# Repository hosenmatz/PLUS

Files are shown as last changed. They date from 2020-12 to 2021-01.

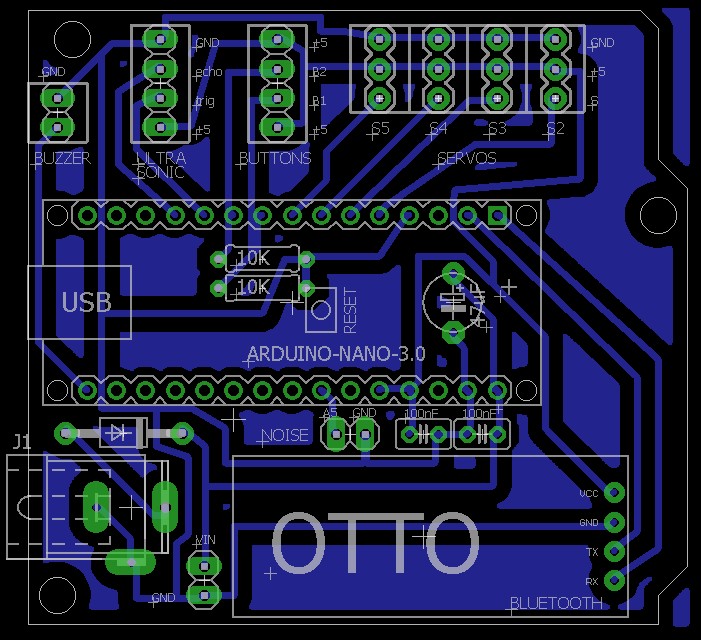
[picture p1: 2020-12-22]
PCB/PCB.jpg

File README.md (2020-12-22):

based on Arduino Nano clone from PRC

based on OTTO firmware v9

the PCB is a single sided PCB to be milled by a cnc with only THD-parts (CADSoft Eagle)

the serial connection is commented out because Bluetooth module is using the RX/TX Pins - means no controlling by wire

this way it is working with the OTTO DIY App now

<a title="bq, CC BY-SA 4.0 &lt;https://creativecommons.org/licenses/by-sa/4.0&gt;, via Wikimedia Commons" href="https://commons.wikimedia.org/wiki/File:Arduino-nano-pinout.png">Arduino-nano-pinout</a>

###

# Otto DIY+ (PLUS)

Special thanks to all these #Ottobuilder that made and are making this project evolve and accessible to everyoone in the world.

## License CC-BY-SA
<br /><span xmlns:dct="http://purl.org/dc/terms/" property="dct:title">Otto DIY</span> by <a xmlns:cc="http://creativecommons.org/ns#"  property="cc:attributionName"> [www.ottodiy.com](http://www.ottodiy.com) </a> is licensed under a <a rel="license" href="http://creativecommons.org/licenses/by-sa/4.0/">Creative Commons Attribution-ShareAlike 4.0 International License</a>.

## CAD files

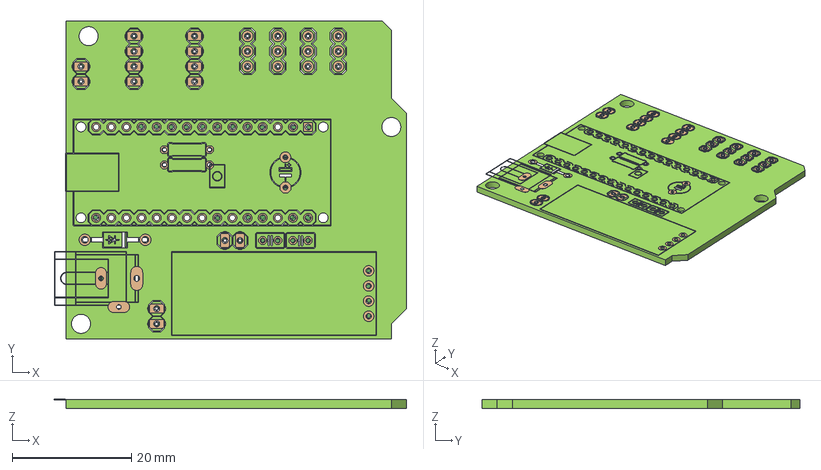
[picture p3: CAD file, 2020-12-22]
PCB/otto_single_sided.FCStd
59.1 x 53.3 x 1.57 mm
Board
Bottom_16
tPad_17
bPad_18
tPlace_21
tDocu_51

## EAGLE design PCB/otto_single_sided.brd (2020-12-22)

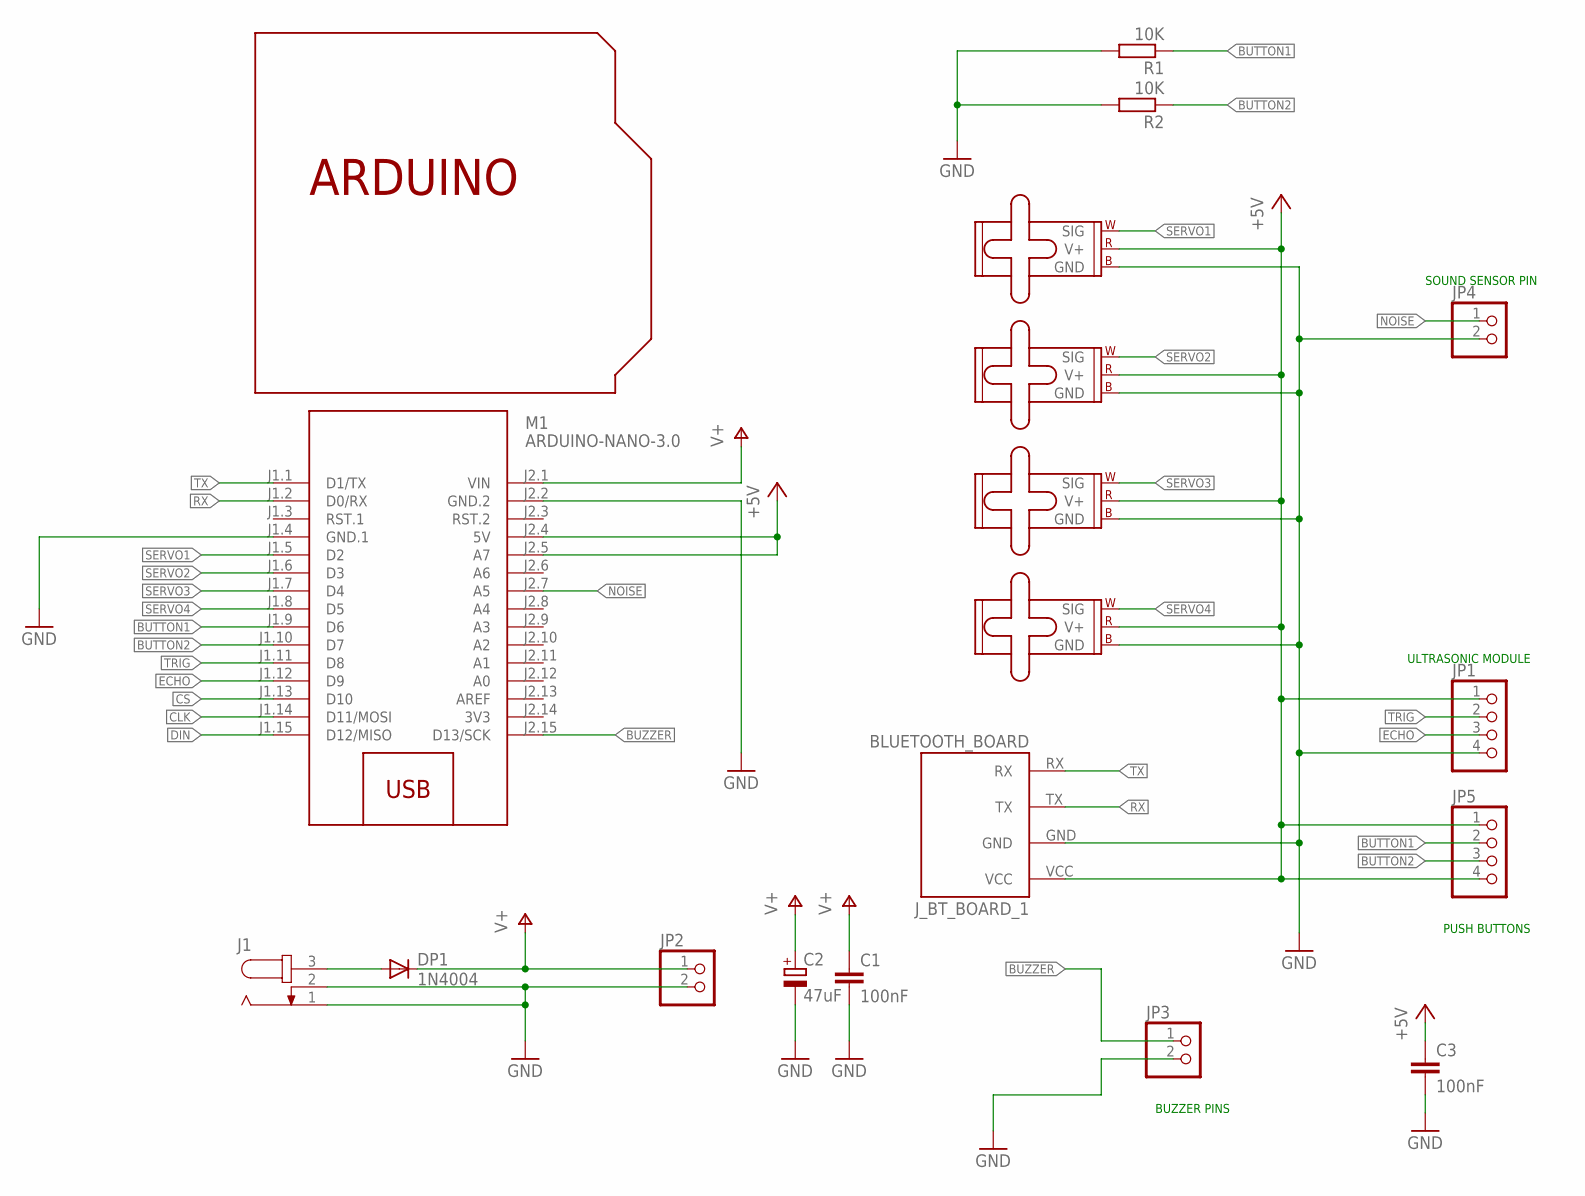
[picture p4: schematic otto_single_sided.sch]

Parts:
C1, C3: 100nF; C025-025X050
C2: 47uF; E5-5
DP1: 1N4004; DO41-10
J1: JACK-PLUG0; SPC4077
JP1, JP5: PINHD-1X4; 1X04
JP2, JP3, JP4: PINHD-1X2; 1X02
J_BT_BOARD_1: BLUETOOTH_BOARD; BT_BOARD_FOOTPRINT
M1: ARDUINO-NANO-3.0
M2, M3, M4, M5: SMALL_SERVO; 1X03
R1, R2: 10K; 0207/7
U$1: SHIELDSMALL; ARDUINOSHIELDSMALL

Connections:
3V3: M1.J2.14 (3V3)
+5V: C3.1, JP1.1, JP5.1, JP5.4, J_BT_BOARD_1.VCC, M1.J2.4 (5V), M1.J2.5 (A7), M2.2 (V+), M3.2 (V+), M4.2 (V+), M5.2 (V+)
BUTTON1: JP5.2, M1.J1.9 (D6), R1.1
BUTTON2: JP5.3, M1.J1.10 (D7), R2.1
BUZZER: JP3.1, M1.J2.15 (D13/SCK)
CLK: M1.J1.14 (D11/MOSI)
CS: M1.J1.13 (D10)
DIN: M1.J1.15 (D12/MISO)
ECHO: JP1.3, M1.J1.12 (D9)
GND: C1.2, C2.-, C3.2, J1.1, J1.2, JP1.4, JP2.2, JP3.2, JP4.2, J_BT_BOARD_1.GND, M1.J1.4 (GND.1), M1.J2.2 (GND.2), M2.3 (GND), M3.3 (GND), M4.3 (GND), M5.3 (GND), R1.2, R2.2
unnamed: DP1.A, J1.3
NOISE: JP4.1, M1.J2.7 (A5)
RX: J_BT_BOARD_1.TX, M1.J1.2 (D0/RX)
SERVO1: M1.J1.5 (D2), M2.1 (SIG)
SERVO2: M1.J1.6 (D3), M3.1 (SIG)
SERVO3: M1.J1.7 (D4), M4.1 (SIG)
SERVO4: M1.J1.8 (D5), M5.1 (SIG)
TRIG: JP1.2, M1.J1.11 (D8)
TX: J_BT_BOARD_1.RX, M1.J1.1 (D1/TX)
V+: C1.1, C2.+, DP1.C, JP2.1, M1.J2.1 (VIN)

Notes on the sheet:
ULTRASONIC MODULE
PUSH BUTTONS
SOUND SENSOR PIN
BUZZER PINS

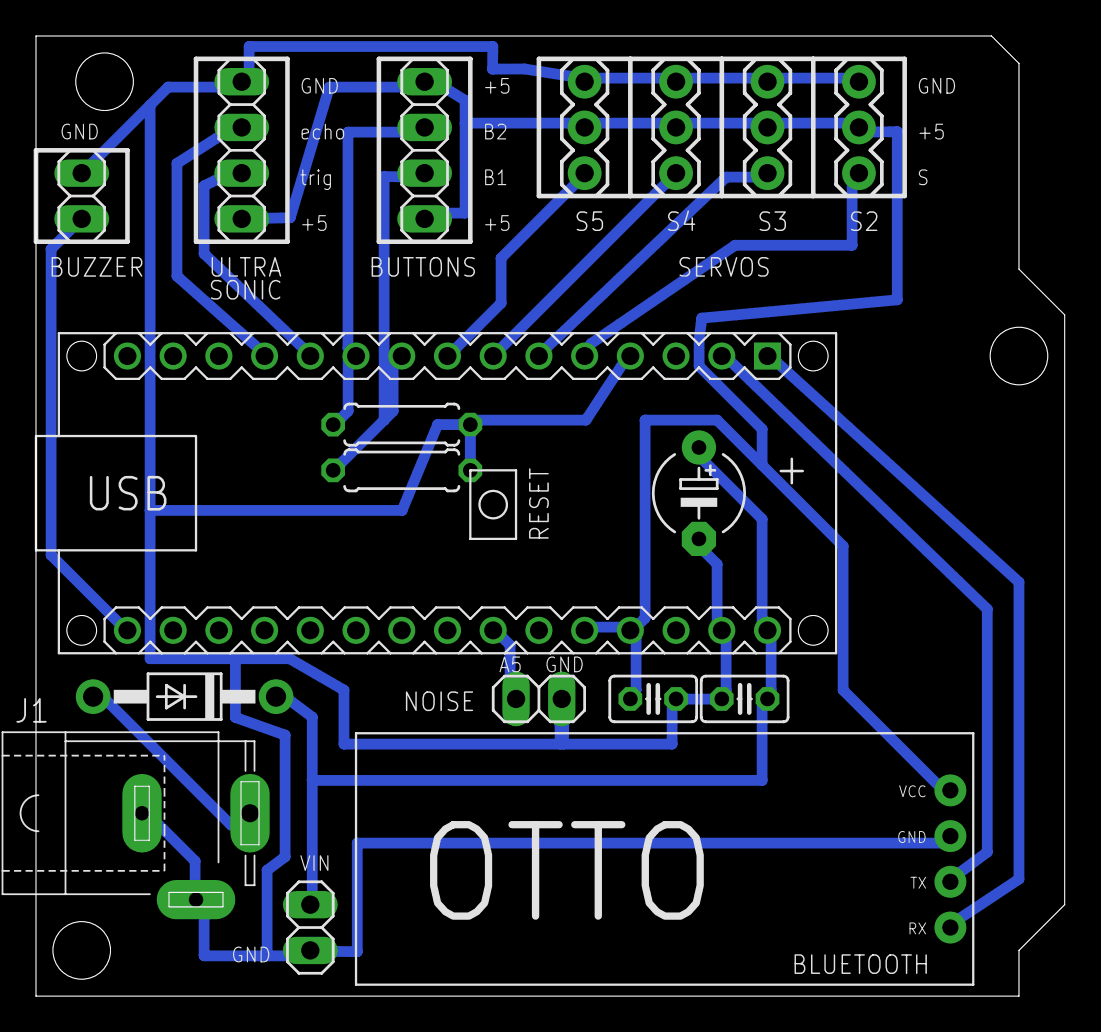
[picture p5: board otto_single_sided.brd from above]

Board: 2 copper layers, 57.2 x 53.3 mm, 19 parts (0 on the bottom side), 16 nets.

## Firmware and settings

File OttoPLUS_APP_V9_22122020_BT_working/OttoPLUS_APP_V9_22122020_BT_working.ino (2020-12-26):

//--------------------------------------------------------------------------------------------------------------------------------------------------------------------
//-- Otto DIY APP Firmware version 9 (V9) with standard baudrate of 9600 for Bluetooth modules.
//-- This code will have all modes and functions therefore memory is almost full but ignore the alert it works perfectly.
//-- Designed to work with the basic Otto or PLUS or Humanoid or other biped robots. some of these functions will need a good power source such as a LIPO battery.
//-- Otto DIY invests time and resources providing open source code and hardware,  please support by purchasing kits from (https://www.ottodiy.com)
//-----------------------------------------------------------------
//-- If you wish to use this software under Open Source Licensing, you must contribute all your source code to the community and all text above must be included in any redistribution
//-- in accordance with the GPL Version 2 when your application is distributed. See http://www.gnu.org/copyleft/gpl.html
//---------------------------------------------------------------------------------------------------------------------------------------------------------------------
// -- ADDED Progmem for MOUTHS and GESTURES: Paul Van De Veen October 2018
// -- ADDED PIN definitions for ease of use: Jason Snow November 2018
// -- ADDED Eye Matrix Progmem and control: Jason Snow November 2018
// -- REMOVED Eye Matrix Progmem and control: Jason Snow AUG 2019
// -- ADDED Battery meassurementin in mode 3 Jason Snow August 2019
// -- ADDED changed to original Software serial library Camilo Parra May 2020
// -- DELETED interrupts and modes to use BTserial Camilo Parra May 2020
//-------------------------------------------------------------------------
#include <EEPROM.h>
#include <SerialCommand.h>//-- Library to manage serial commands

//SoftwareSerial auskommentiert, da BT und Software die gleichen Ports teilen (RX/TX auf singlesided PCB auf dem Nano)
  //SoftwareSerial BTserial = SoftwareSerial(1,0); //  TX  RX of the Bluetooth - SoftwareSerial(rxPin, txPin, inverse_logic)
  //SerialCommand SCmd(BTserial);  //The SerialCommand object

SerialCommand SCmd;  //The SerialCommand object
#include <Otto9.h>
Otto9 Otto;  //This is Otto!
/*             -------- 
              |  O  O  |
              |--------|
  RIGHT LEG 3 |        | LEFT LEG 2
               -------- 
               ||     ||
RIGHT FOOT 5 |---     ---| LEFT FOOT 4    
*/ 
// SERVO PINs //////////////////////////////////////////////////////////////////////////////
#define PIN_YL 2 //servo[0]  left leg
#define PIN_YR 3 //servo[1]  right leg
#define PIN_RL 4 //servo[2]  left foot
#define PIN_RR 5 //servo[3]  right foot
// ULTRASONIC PINs /////////////////////////////////////////////////////////////////////////
#define PIN_Trigger  8  //TRIGGER pin (8)
#define PIN_Echo     9  //ECHO pin (9)
// BUZZER PIN //////////////////////////////////////////////////////////////////////////////
#define PIN_Buzzer  13 //BUZZER pin (13)
// SOUND SENSOR PIN //////////////////////////////////////////////////////////////////////////
#define PIN_NoiseSensor A6  //SOUND SENSOR   ANALOG pin (A6)
// LED MATRIX PINs //////////////////////////////////////////////////////////////////////////
#define DIN_PIN    A3   //DIN pin (A3)
#define CS_PIN     A2   //CS pin (A2)
#define CLK_PIN    A1   //CLK pin (A1)
#define LED_DIRECTION  1// LED MATRIX CONNECTOR position (orientation) 1 = top 2 = bottom 3 = left 4 = right  DEFAULT = 1
// BATTERY SENSE PIN //////////////////////////////////////////////////////////////////////////
boolean BATTcheck = false;    // SET TO FALSE IF NOT USING THIS OPTION
#define PIN_Battery   A7  //3v7 BATTERY MONITOR   ANALOG pin (A7)
// TOUCH SENSOR or PUSH BUTTON /////////////////////////////////////////////////////////////////
#define PIN_Button   A0 // TOUCH SENSOR Pin (A0) PULL DOWN RESISTOR MAYBE REQUIRED to stop false interrupts (interrupt PIN)
// SERVO ASSEMBLY PIN   /////////////////////////////////////////////////////////////////////
// to help assemble Otto's feet and legs - wire link between pin 10 and GND
#define PIN_ASSEMBLY    10   //ASSEMBLY pin (10) LOW = assembly    HIGH  = normal operation
///////////////////////////////////////////////////////////////////
//-- Global Variables -------------------------------------------//
///////////////////////////////////////////////////////////////////

const char programID[] = "OttoPLUS_V9"; //Each program will have a ID
const char name_fac = '$'; //Factory name
const char name_fir = '#'; //First name
//-- Movement parameters
int T = 1000;            //Initial duration of movement
int moveId = 0;          //Number of movement
int moveSize = 15;       //Asociated with the height of some movements
volatile bool buttonPushed=false;  //Variable to remember when a button has been pushed
unsigned long previousMillis = 0;
int randomDance = 0;
int randomSteps = 0;
bool obstacleDetected = false;
double batteryCHECK = 0;
unsigned long int matrix;
unsigned long timerMillis = 0;
///////////////////////////////////////////////////////////////////
//-- Setup ------------------------------------------------------//
///////////////////////////////////////////////////////////////////
void setup() {
  //Serial communication initialization
  Serial.begin(9600);
  //SoftwareSerial auskommentiert, da BT und Software die gleichen Ports teilen (RX/TX auf singlesided PCB auf dem Nano)
  //BTserial.begin(9600);

  Serial.println("AT+DISC");
  
  Otto.init(PIN_YL, PIN_YR, PIN_RL, PIN_RR, true, PIN_NoiseSensor, PIN_Buzzer, PIN_Trigger, PIN_Echo); //Set the servo pins and ultrasonic pins
  Otto.initMATRIX( DIN_PIN, CS_PIN, CLK_PIN, LED_DIRECTION);   // set up Matrix display pins = DIN pin,CS pin, CLK pin, MATRIX orientation 
  Otto.matrixIntensity(1);// set up Matrix display intensity
  Otto.initBatLevel(PIN_Battery);// set up Battery percent read pin - MUST BE AN ANALOG PIN
  randomSeed(analogRead(PIN_NoiseSensor));   //Set a random seed
  pinMode(PIN_ASSEMBLY,INPUT_PULLUP); // - Easy assembly pin - LOW is assembly Mode
  pinMode(PIN_Button,INPUT); // - ensure pull-down resistors are used

  //Setup callbacks for SerialCommand commands
  SCmd.addCommand("S", receiveStop);      //  sendAck & sendFinalAck
  SCmd.addCommand("L", receiveLED);       //  sendAck & sendFinalAck
  SCmd.addCommand("T", recieveBuzzer);    //  sendAck & sendFinalAck
  SCmd.addCommand("M", receiveMovement);  //  sendAck & sendFinalAck
  SCmd.addCommand("H", receiveGesture);   //  sendAck & sendFinalAck
  SCmd.addCommand("K", receiveSing);      //  sendAck & sendFinalAck
  SCmd.addCommand("J", receiveMode);      //  sendAck & sendFinalAck
  SCmd.addCommand("C", receiveTrims);     //  sendAck & sendFinalAck
  SCmd.addCommand("G", receiveServo);     //  sendAck & sendFinalAck
  SCmd.addCommand("R", receiveName);      //  sendAck & sendFinalAck
  SCmd.addCommand("E", requestName);
  SCmd.addCommand("D", requestDistance);
  SCmd.addCommand("N", requestNoise);
  SCmd.addCommand("B", requestBattery);   // 3v7 lipo battery
  SCmd.addCommand("I", requestProgramId);
  SCmd.addDefaultHandler(receiveStop);
  //Otto wake up!
  Otto.sing(S_connection);
  Otto.home();
  // Animation Uuuuuh - A little moment of initial surprise
  //-----
  for (int i = 0; i < 2; i++) {
    for (int i = 0; i < 8; i++) {
      Otto.putAnimationMouth(littleUuh, i);
      delay(150);
    }
  }
  //Smile for a happy Otto :)
  Otto.putMouth(smile);
  Otto.sing(S_happy);
  delay(200);

  //If Otto's name is '#' means that Otto hasn't been baptized
  //In this case, Otto does a longer greeting
  //5 = EEPROM address that contains first name character
  if (EEPROM.read(5) == name_fir) {
    Otto.jump(1, 700);
    delay(200);
    Otto.shakeLeg(1, T, 1);
    Otto.putMouth(smallSurprise);
    Otto.swing(2, 800, 20);
    Otto.home();
  }

  Otto.putMouth(happyOpen);
  previousMillis = millis();
// if Pin 10 is LOW then place OTTO's servos in home mode to enable easy assembly, 
// when you have finished assembling Otto, remove the link between pin 10 and GND
  while (digitalRead(PIN_ASSEMBLY) == LOW) {
    Otto.home();
    Otto.sing(S_happy_short);   // sing every 5 seconds so we know OTTO is still working
    delay(5000);
  }
}
///////////////////////////////////////////////////////////////////
//-- Principal Loop ---------------------------------------------//
///////////////////////////////////////////////////////////////////
void loop() {
        SCmd.readSerial();    //If Otto is moving yet
        if (Otto.getRestState()==false){  
          move(moveId);
        }  
    }

///////////////////////////////////////////////////////////////////
//-- Functions --------------------------------------------------//
///////////////////////////////////////////////////////////////////

//-- Function to read distance sensor & to actualize obstacleDetected variable
void obstacleDetector() {
  int distance = Otto.getDistance();
  if (distance < 15) obstacleDetected = true;
  else obstacleDetected = false;
}

//-- Function to receive Stop command.
void receiveStop() {
  sendAck();
  Otto.home();
  sendFinalAck();
}

//-- Function to receive LED commands
void receiveLED() {

  //sendAck & stop if necessary
  sendAck();
  Otto.home();
  unsigned long int matrix;
  char *arg;
  char *endstr;
  arg = SCmd.next(); //Serial.println (arg);
  if (arg != NULL) {
    matrix = strtoul(arg, &endstr, 2); // Converts a char string to unsigned long integer
    Otto.putMouth(matrix, false);
  }
  else {
    Otto.putMouth(xMouth);
    delay(2000);
    Otto.clearMouth();
  }
  sendFinalAck();
}

//-- Function to receive buzzer commands
void recieveBuzzer() {
  //sendAck & stop if necessary
  sendAck();
  Otto.home();

  bool error = false;
  int frec;
  int duration;
  char *arg;

  arg = SCmd.next();
  if (arg != NULL) frec = atoi(arg);  // Converts a char string to an integer
  else error = true;

  arg = SCmd.next();
  if (arg != NULL) duration = atoi(arg);  // Converts a char string to an integer
  else error = true;
  if (error == true) {
    Otto.putMouth(xMouth);
    delay(2000);
    Otto.clearMouth();
  }
  else Otto._tone(frec, duration, 1);
  sendFinalAck();
}

//-- Function to receive TRims commands
void receiveTrims() {
  //sendAck & stop if necessary
  sendAck();
  Otto.home();
  int trim_YL, trim_YR, trim_RL, trim_RR;

  //Definition of Servo Bluetooth command
  //C trim_YL trim_YR trim_RL trim_RR
  //Examples of receiveTrims Bluetooth commands
  //C 20 0 -8 3
  bool error = false;
  char *arg;
  arg = SCmd.next();
  if (arg != NULL) trim_YL = atoi(arg);  // Converts a char string to an integer
  else error = true;

  arg = SCmd.next();
  if (arg != NULL) trim_YR = atoi(arg);  // Converts a char string to an integer
  else error = true;

  arg = SCmd.next();
  if (arg != NULL) trim_RL = atoi(arg);  // Converts a char string to an integer
  else error = true;

  arg = SCmd.next();
  if (arg != NULL) trim_RR = atoi(arg);  // Converts a char string to an integer
  else error = true;
  if (error == true) {
    Otto.putMouth(xMouth);
    delay(2000);
    Otto.clearMouth();

  } else { //Save it on EEPROM
    Otto.setTrims(trim_YL, trim_YR, trim_RL, trim_RR);
    Otto.saveTrimsOnEEPROM(); //Uncomment this only for one upload when you finaly set the trims.
  }
  sendFinalAck();
}

//-- Function to receive Servo commands
void receiveServo() {
  sendAck();
  moveId = 30;

  //Definition of Servo Bluetooth command
  //G  servo_YL servo_YR servo_RL servo_RR
  //Example of receiveServo Bluetooth commands
  //G 90 85 96 78
  bool error = false;
  char *arg;
  int servo_YL, servo_YR, servo_RL, servo_RR;

  arg = SCmd.next();
  if (arg != NULL) servo_YL = atoi(arg);  // Converts a char string to an integer
  else error = true;

  arg = SCmd.next();
  if (arg != NULL) servo_YR = atoi(arg);  // Converts a char string to an integer
  else error = true;

  arg = SCmd.next();
  if (arg != NULL) servo_RL = atoi(arg);  // Converts a char string to an integer
  else error = true;

  arg = SCmd.next();
  if (arg != NULL) {
    servo_RR = atoi(arg);  // Converts a char string to an integer
  }
  else error = true;
  if (error == true) {
    Otto.putMouth(xMouth);
    delay(2000);
    Otto.clearMouth();
  }
  else { //Update Servo:
    int servoPos[4] = {servo_YL, servo_YR, servo_RL, servo_RR};
    Otto._moveServos(200, servoPos);   //Move 200ms
  }
  sendFinalAck();
}

//-- Function to receive movement commands
void receiveMovement() {
  sendAck();
  if (Otto.getRestState() == true) Otto.setRestState(false);

  //Definition of Movement Bluetooth commands
  //M  MoveID  T   MoveSize
  char *arg;
  arg = SCmd.next();
  if (arg != NULL) moveId = atoi(arg);
  else {
    Otto.putMouth(xMouth);
    delay(2000);
    Otto.clearMouth();
    moveId = 0; //stop
  }
  arg = SCmd.next();
  if (arg != NULL) T = atoi(arg);
  else T = 1000;
  arg = SCmd.next();
  if (arg != NULL) moveSize = atoi(arg);
  else moveSize = 15;
}

//-- Function to execute the right movement according the movement command received.
void move(int moveId) {
  bool manualMode = false;

  switch (moveId) {
    case 0:
      Otto.home();
      break;
    case 1: //M 1 1000
      Otto.walk(1, T, 1);
      break;
    case 2: //M 2 1000
      Otto.walk(1, T, -1);
      break;
    case 3: //M 3 1000
      Otto.turn(1, T, 1);
      break;
    case 4: //M 4 1000
      Otto.turn(1, T, -1);
      break;
    case 5: //M 5 1000 30
      Otto.updown(1, T, moveSize);
      break;
    case 6: //M 6 1000 30
      Otto.moonwalker(1, T, moveSize, 1);
      break;
    case 7: //M 7 1000 30
      Otto.moonwalker(1, T, moveSize, -1);
      break;
    case 8: //M 8 1000 30
      Otto.swing(1, T, moveSize);
      break;
    case 9: //M 9 1000 30
      Otto.crusaito(1, T, moveSize, 1);
      break;
    case 10: //M 10 1000 30
      Otto.crusaito(1, T, moveSize, -1);
      break;
    case 11: //M 11 1000
      Otto.jump(1, T);
      break;
    case 12: //M 12 1000 30
      Otto.flapping(1, T, moveSize, 1);
      break;
    case 13: //M 13 1000 30
      Otto.flapping(1, T, moveSize, -1);
      break;
    case 14: //M 14 1000 20
      Otto.tiptoeSwing(1, T, moveSize);
      break;
    case 15: //M 15 500
      Otto.bend(1, T, 1);
      break;
    case 16: //M 16 500
      Otto.bend(1, T, -1);
      break;
    case 17: //M 17 500
      Otto.shakeLeg(1, T, 1);
      break;
    case 18: //M 18 500
      Otto.shakeLeg(1, T, -1);
      break;
    case 19: //M 19 500 20
      Otto.jitter(1, T, moveSize);
      break;
    case 20: //M 20 500 15
      Otto.ascendingTurn(1, T, moveSize);
      break;
    default:
      manualMode = true;
      break;
  }
  if (!manualMode) sendFinalAck();
}

//-- Function to receive gesture commands
void receiveGesture() {
  //sendAck & stop if necessary
  sendAck();
  Otto.home();

  //Definition of Gesture Bluetooth commands
  //H  GestureID
  int gesture = 0;
  char *arg;
  arg = SCmd.next();
  if (arg != NULL) gesture = atoi(arg);
  else     delay(2000); //Otto.putMouth(xMouth); //Otto.clearMouth();

  switch (gesture) {
    case 1: //H 1
      Otto.playGesture(OttoHappy);
      break;
    case 2: //H 2
      Otto.playGesture(OttoSuperHappy);
      break;
    case 3: //H 3
      Otto.playGesture(OttoSad);
      break;
    case 4: //H 4
      Otto.playGesture(OttoSleeping);
      break;
    case 5: //H 5
      Otto.playGesture(OttoFart);
      break;
    case 6: //H 6
      Otto.playGesture(OttoConfused);
      break;
    case 7: //H 7
      Otto.playGesture(OttoLove);
      break;
    case 8: //H 8
      Otto.playGesture(OttoAngry);
      break;
    case 9: //H 9
      Otto.playGesture(OttoFretful);
      break;
    case 10: //H 10
      Otto.playGesture(OttoMagic);
      break;
    case 11: //H 11
      Otto.playGesture(OttoWave);
      break;
    case 12: //H 12
      Otto.playGesture(OttoVictory);
      break;
    case 13: //H 13
      Otto.playGesture(OttoFail);
      break;
    default:
      break;
  }
  sendFinalAck();
}

//-- Function to receive sing commands
void receiveSing() {
  //sendAck & stop if necessary
  sendAck();
  Otto.home();

  //Definition of Sing Bluetooth commands
  //K  SingID
  int sing = 0;
  char *arg;
  arg = SCmd.next();
  if (arg != NULL) sing = atoi(arg);
  else     delay(2000); // Otto.putMouth(xMouth); //Otto.clearMouth();

  switch (sing) {
    case 1: //K 1
      Otto.sing(S_connection);
      break;
    case 2: //K 2
      Otto.sing(S_disconnection);
      break;
    case 3: //K 3
      Otto.sing(S_surprise);
      break;
    case 4: //K 4
      Otto.sing(S_OhOoh);
      break;
    case 5: //K 5
      Otto.sing(S_OhOoh2);
      break;
    case 6: //K 6
      Otto.sing(S_cuddly);
      break;
    case 7: //K 7
      Otto.sing(S_sleeping);
      break;
    case 8: //K 8
      Otto.sing(S_happy);
      break;
    case 9: //K 9
      Otto.sing(S_superHappy);
      break;
    case 10: //K 10
      Otto.sing(S_happy_short);
      break;
    case 11: //K 11
      Otto.sing(S_sad);
      break;
    case 12: //K 12
      Otto.sing(S_confused);
      break;
    case 13: //K 13
      Otto.sing(S_fart1);
      break;
    case 14: //K 14
      Otto.sing(S_fart2);
      break;
    case 15: //K 15
      Otto.sing(S_fart3);
      break;
    case 16: //K 16
      Otto.sing(S_mode1);
      break;
    case 17: //K 17
      Otto.sing(S_mode2);
      break;
    case 18: //K 18
      Otto.sing(S_mode3);
      break;
    case 19: //K 19
      Otto.sing(S_buttonPushed);
      break;
    default:
      break;
  }
  sendFinalAck();
}

//-- Function to receive mode selection.
void receiveMode() {
  sendAck();
  Otto.home();
  //Definition of Mode Bluetooth commands
  //J ModeID
  int modeId = 0; 
  char *arg;
  arg = SCmd.next();
  if (arg != NULL) modeId = atoi(arg);
  else     delay(2000);
  
  switch (modeId) {
    case 0: // J 0
    Otto.putMouth(0);
    Otto.sing(S_cuddly);
    Otto.home();
      break;
    case 1: // J 1 
    Otto.putMouth(one);
     randomDance = random(5, 21); //5,20
      if ((randomDance > 14) && (randomDance < 19)) {
        randomSteps = 1;
        T = 1600;
      }
      else {
        randomSteps = random(3, 6); //3,5
        T = 1000;
      }
      Otto.putMouth(random(10, 21));
      for (int i = 0; i < randomSteps; i++) move(randomDance);
      break;
    case 2: // J 2
      Otto.putMouth(two);
      break;
    case 3: //J 3
      Otto.putMouth(three);
      break;
    case 4: //J 4
      Otto.putMouth(four);
  if (Otto.getBatteryLevel() < 35) {
    Otto.putMouth(thunder);
    Otto.bendTones (880, 2000, 1.04, 8, 3);  //A5 = 880
    delay(30);
    Otto.bendTones (2000, 880, 1.02, 8, 3);  //A5 = 880
    delay(30);
    Otto.bendTones (880, 2000, 1.04, 8, 3);  //A5 = 880
    delay(30);
    Otto.bendTones (2000, 880, 1.02, 8, 3);  //A5 = 880
    Otto.clearMouth();
    matrix = 0b00001100010010010010010010011110; // show empty battery symbol
     Otto.putMouth(matrix, false);
    delay(2000);
    Otto.clearMouth();
     delay(1000);
    matrix = 0b00001100010010010010010010011110; // show empty battery symbol
    Otto.putMouth(matrix, false);
    delay(2000);
    Otto.clearMouth();
    Otto.putMouth(happyOpen);
  }    
      break;
    default:
      break;
  }
  sendFinalAck();
}

//-- Function to receive Name command
void receiveName() {
  //sendAck & stop if necessary
  sendAck();
  Otto.home();
  char newOttoName[11] = "";  //Variable to store data read from Serial.
  int eeAddress = 5;          //Location we want the data to be in EEPROM.
  char *arg;
  arg = SCmd.next();
  if (arg != NULL) {
    //Complete newOttoName char string
    int k = 0;
    while ((*arg) && (k < 11)) {
      newOttoName[k] = *arg++;
      k++;
    }
    EEPROM.put(eeAddress, newOttoName);
  }
  else
  {
    //Otto.putMouth(xMouth);
    delay(2000);
    //Otto.clearMouth();
  }
  sendFinalAck();
}

//-- Function to send Otto's name
void requestName() {
  Otto.home(); //stop if necessary
  char actualOttoName[11] = ""; //Variable to store data read from EEPROM.
  int eeAddress = 5;            //EEPROM address to start reading from
  //Get the float data from the EEPROM at position 'eeAddress'
  EEPROM.get(eeAddress, actualOttoName);

  Serial.print(F("&&"));
  Serial.print(F("E "));
  Serial.print(actualOttoName);
  Serial.println(F("%%"));
  Serial.flush();
}

//-- Function to send ultrasonic sensor measure (distance in "cm")
void requestDistance() {
  Otto.home();  //stop if necessary
  int distance = Otto.getDistance();
  Serial.print(F("&&"));
  Serial.print(F("D "));
  Serial.print(distance);
  Serial.println(F("%%"));
  Serial.flush();
}

//-- Function to send noise sensor measure
void requestNoise() {
  Otto.home();  //stop if necessary
  int microphone = Otto.getNoise(); //analogRead(PIN_NoiseSensor);
  Serial.print(F("&&"));
  Serial.print(F("N "));
  Serial.print(microphone);
  Serial.println(F("%%"));
  Serial.flush();
}

//-- Function to send battery voltage percent
void requestBattery() {
  Otto.home();  //stop if necessary
  //The first read of the battery is often a wrong reading, so we will discard this value.
  double batteryLevel = Otto.getBatteryLevel();
  Serial.print(F("&&"));
  Serial.print(F("B "));
  Serial.print(batteryLevel);
  Serial.println(F("%%"));
  Serial.flush();
}

//-- Function to send program ID
void requestProgramId() {
  Otto.home();   //stop if necessary
  Serial.print(F("&&"));
  Serial.print(F("I "));
  Serial.print(programID);
  Serial.println(F("%%"));
  Serial.flush();
}

//-- Function to send Ack comand (A)
void sendAck() {
  delay(30);
  Serial.print(F("&&"));
  Serial.print(F("A"));
  Serial.println(F("%%"));
  Serial.flush();
}

//-- Function to send final Ack comand (F)
void sendFinalAck() {
  delay(30);
  Serial.print(F("&&"));
  Serial.print(F("F"));
  Serial.println(F("%%"));
  Serial.flush();
}
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

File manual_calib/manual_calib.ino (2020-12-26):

#include <Otto9.h>
Otto9 Otto;

#define PIN_YL 2 // left leg, servo[0]
#define PIN_YR 3 // right leg, servo[1]
#define PIN_RL 4 // left foot, servo[2]
#define PIN_RR 5 // right foot, servo[3]
#define PIN_Trigger 8 // ultrasound
#define PIN_Echo 9 // ultrasound
#define PIN_Buzzer  13 //buzzer

#define LeftLeg -15
#define RightLeg -15

#define LeftFoot -20
#define RightFoot 25

void setup() {
  Otto.init(PIN_YL, PIN_YR, PIN_RL, PIN_RR, true, A6, PIN_Buzzer, PIN_Trigger, PIN_Echo);
  Otto.setTrims(LeftLeg,RightLeg,LeftFoot,RightFoot);
  //Otto.setTrims(-15,0,0,15);
 Otto.saveTrimsOnEEPROM();
    // Change the legs and feet values gradually with small values and increments(+5 or - 5 degrees)
  //
  // Iteratively you have to check/upload the code multiple times, until Otto legs and feet looks completely straight.
  //calibrated
  // ONLY after the robot looks straight you can activate this block, then disable or delete again for further programming, otherwise can leave permanent damage in the memory. BE CAREFUL
  //calibration saved

}

void loop() {
    Otto.home();
    delay(4000);
    Otto.walk(5);
}

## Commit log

2018-05-10 Arduino sketch for APP
    by Jason Snow
2018-05-10 Arduino sketch for APP
2018-06-04 according to manual
    [OttoDIY+_Leg_v06.stl, OttoDIY+_body_v06.stl, OttoDIY+_foot_v06.stl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]
2018-07-04 PCB tests
    [OTTO-BOM version L(3).xlsx, OTTO-BOM version L(4).xlsx, OTTO-BOM version L.xlsx]
2018-09-19 3D STL update
    [OttoDIY+_Leg_v07.stl, OttoDIY+_body_v07.stl, OttoDIY+_head_v07.stl]
2018-10-04 added single sided board
    removed MAX7219 to get it routetd as single sided board for my cnc router
    [otto_single_sided.brd, otto_single_sided.sch]
2018-10-04 connected R1 GND Point
    R1 was not connected to GND
    [otto_single_sided.brd, otto_single_sided.sch]
2020-12-22 cleaned some files
    [OTTO-BOM version L(3).xlsx, OTTO-BOM version L(4).xlsx, OTTO-BOM version L.xlsx]
2020-12-22 added pcb pic

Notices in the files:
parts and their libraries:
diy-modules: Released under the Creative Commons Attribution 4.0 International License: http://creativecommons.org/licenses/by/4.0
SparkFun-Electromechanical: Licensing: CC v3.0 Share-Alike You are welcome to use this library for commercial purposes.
